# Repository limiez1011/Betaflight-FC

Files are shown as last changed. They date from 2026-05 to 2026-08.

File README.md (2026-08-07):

# yecnod F405 V1.1

## Description

open-source (not that anyone would want to use it) 40x40 F405 Flight controller using betaflight software.
## Features

- 3 Universal UARTS
- Dedicated pads for analog VTX
- 9V and 5V Buck converters
- 2x 3.3V LDOS
- Integrated barometer
- LDO and Buck converter status LEDS
- 16MB Blackbox flash
- Full betaflight support
- ICM 42688-P (kind of a flex with how hard they are to get nowadays)
- 4V5 Pads for RX

This is the first revision of the yecnodF405 so expect more features on the 2nd.

[Schematic PDF](https://github.com/user-attachments/files/29501861/20x20.fc.pdf)

## COST

- AROUND 60 USD PER PCB
- AROUND 30 USD FOR 5 PCBS

On my next revision I will try to cut the costs by atleast 40%

## BOM

| | NAME | PURPOSE | QTY | PRICE  | LINK |
|---|---|---|-----|---|---|
| 1 | LCSC | PASSIVES/ALL IC'S | 1 | $73.43 | [LINK](https://www.lcsc.com) |
| 2 | HOT AIR GUN | SOLDERING | 1 | $35 | [LINK](https://www.emag.ro/fier-de-lipit-torta-cu-aer-cald-yihua-8858-iv-a5dc-582e4/pd/D3JM2VYBM/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) |
| 3 | MP4420 | BUCK CONVERTER (NOT AVAILABLE ON LCSC) | 10  | $7.7 | [LINK](https://www.aliexpress.com/item/1005009928983923.html?spm=a2g0o.cart.0.0.2e1938damlvGFl&mp=1) |
| 4 | TWEEZERS | HELP FOR SOLDERING TINY 0402 | 2 | $16.5  | [LINK](https://www.aliexpress.com/item/1005007691201333.html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) [LINK](https://www.aliexpress.com/item/1005008389644631.html?spm=a2g0o.cart.0.0.2e1938damlvGFl&mp=1) |
| 5 | FLUX | SOLDERING | 1 | $11.2  | [LINK](https://www.aliexpress.com/item/1005008666080401.html?spm=a2g0o.cart.0.0.2e1938damlvGFl&mp=1) |
| 6 | C245 TIP | SOLDERING | 1 | $7 | [LINK](https://www.aliexpress.com/item/1005008666080401.html?spm=a2g0o.cart.0.0.2e1938damlvGFl&mp=1) |
| 7 | JLCPCB | PCBS | 5 | $12.71 | [LINK](https://jlcpcb.com/) |
| 8 | TARIFFS | dumb eu laws | 1 | $41 | |

Final prices for each website are available as screenshots on the macondo website. LCSC cart BOM is available as a csv. 
Total price for everything is 204.73 USD
## Notes

- This is my 2nd ever electronics project (Although I made another 3 during the break I took on this project) so don't expect everything to be electrically sound, this has been a great learning experience though, even with all the headaches it gave me.
- The jlcpcb BOM is only partly complete since I've decided to not use PCBA (use at you own risk some parts may not be right)

## Photos






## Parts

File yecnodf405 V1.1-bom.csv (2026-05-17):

Name | Purpose | Quantity | Total Cost (USD) | Link | Distributor
Solder paste | soldering | 1 | 9.00 | https://www.gsmnet.ro/aparatura-instrumente-service-piese-schimb-consumabile/pasta-fludor-relife-rl-406s-tip-seringa | GSMNET.RO
Solder paste squegee | soldering | 1 | 3.00 | https://ro.farnell.com/chip-quik/minisqueege-1/solder-paste-stencil-squeegee/dp/3549325 | Farnell RO
FLUX PASTE | Soldering components | 1 | 13.00 | https://ro.farnell.com/mg-chemicals/8341-10ml/no-clean-flux-paste-10ml-10g/dp/3018420 | Farnell RO
Fnirsi SAG-55 | Hot air station (soldering) | 1 | 68.00 | https://www.fnirsi.com/products/sag-55?variant=46483610796250 | FNIRSI
PCB+stencil | pcbing+stenciling | 5 | 35.00 |  | JLCPCB
JST-SH 8PIN | esc comms | 1 | 1.50 |  | LCSC
INDUCTORS | BUCK CONVERTERS | 2 | 2.70 |  | FARNELL RO
ICM-42688-P | IMU (should have at home | 1 | 0.00 |  | me
PASSIVES TOTAL COST | TOTAL cost of all caps resistors diodes leds | 1 | 8.50 | https://www.lcsc.com/ | LCSC
C25858 | 16.9K | 2 | 0.00
C1985520 | 16Mhz | 1 | 0.62 | https://www.lcsc.com/product-detail/C1985520.html?s_z=n_q_t_ABM11 | LCSC
C11476 | 18.7k | 1 | 0.00
C11702 | 1K | 2 | 0.00
C1518208 | 1uF | 3 | 0.00
C25150 | 20 | 2 | 0.00
C25092 | 22 | 2 | 0.00
C3845593 | 22uF | 1 | 0.00
C86295 | 22uF | 1 | 0.00
C25769 | 24K | 1 | 0.00
C1985480 | 27Mhz | 1 | 1.66 | https://www.lcsc.com/product-detail/C1985480.html?s_z=n_q_t_ABM11 | LCSC
C12530 | 2u2 | 3 | 0.00
C25900 | 4.7K | 3 | 0.00
C2858031 | 4.7uF | 2 | 0.00
C69335 | 4.7uF | 2 | 0.00
C25118 | 47 | 1 | 0.00
C47339 | 470nF | 1 | 0.00
C76659 | 47uF | 1 | 0.00
C25905 | 5.1K | 2 | 0.00
C25904 | 51.1K | 1 | 0.00
C25130 | 680 | 1 | 0.00
C25133 | 75 | 2 | 0.00
C25798 | 75K | 1 | 0.00
C19709 | 86.6K | 1 | 0.00
C270420 | 9.76K | 1 | 0.00
C3194330 | MP4420GJ-P | 2 | 10.00
C15639 | MS561101BA03-50 | 1 | 6.62 | https://www.lcsc.com/product-detail/C15639.html?s_z=n_q_t_MS5611 | LCSC
C25741 | 100K | 7 | 0.00
C25744 | 10k | 1 | 0.00
C1527 | 150pF | 2 | 0.00
C190862 | W25Q128JVPIQ | 2 | 7.21 | https://www.lcsc.com/product-detail/C190862.html?s_z=n_q_W25Q128JVPIQ | LCSC
C165948 | USCBC | 5 | 0.86 | https://www.lcsc.com/product-detail/C165948.html?s_z=n_q_p_USBC%2520HRO | LCSC
C2054141 | STM32F405RGT6 | 1 | 3.97 | https://www.lcsc.com/product-detail/C15742.html?s_z=n_q_STM32F405RGT6 | LCSC
C82351 | AT7456E | 1 | 3.61 | https://www.lcsc.com/product-detail/C82351.html?s_z=s_p_t_AT7456E | LCSC
C2969892 | LDL212PV33R | 2 | 1.30 | https://www.lcsc.com/product-detail/C2969892.html?s_z=n_q_p_LDL12PV33R | LCSC
C10217 | SMBJ28A | 1 | 0.58 | https://www.lcsc.com/product-detail/C178227.html?s_z=n_q_SMBJ28A | LCSC
C25867 | 1.5K | 1 | 0.00
C14663 | 100nF | 2 | 0.00
C24497 | 100nF | 1 | 0.00
C307331 | 100nF | 18 | 0.00
C307331 | 100nf | 2 | 0.00
C25744 | 10K | 4 | 0.00
C15195 | 10nF | 1 | 0.00
C1548 | 15pF | 2 | 0.00

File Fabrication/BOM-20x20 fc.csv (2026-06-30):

Comment | Designator | Footprint | LCSC | Quantity
1.5K | R29 | R_0402_1005Metric | C25867 | 1
100K | R19,R22,R28,R4,R8 | R_0402_1005Metric | C25741 | 5
100nF | C17,C29,C41 | C_0603_1608Metric | C14663 | 3
100nF | C13,C14,C23,C25,C26,C27,C3,C30,C33,C34,C36,C37,C4,C40,C5,C6,C7,C8 | C_0402_1005Metric | C307331 | 18
100nf | C38,C39 | C_0402_1005Metric | C307331 | 2
10K | R13,R26,R27,R30 | R_0402_1005Metric | C25744 | 4
10k | R35 | R_0402_1005Metric | C25744 | 1
10nF | C22 | C_0402_1005Metric | C15195 | 1
12.4K | R20 | R_0402_1005Metric | C11692 | 1
150K | R10 | R_0402_1005Metric | C25755 | 1
15pF | C10,C11 | C_0402_1005Metric | C1548 | 2
16Mhz | Y1 | CRYSTAL-SMD_4P-L2.0-W1.6-BL | C1985520 | 1
18.7K | R7 | R_0402_1005Metric | C11476 | 1
1K | R31,R32 | R_0402_1005Metric | C11702 | 2
1uF | C18,C20,C9 | C_0402_1005Metric | C1518208 | 3
20 | R18,R5 | R_0402_1005Metric | C25150 | 2
22 | R1,R2 | R_0402_1005Metric | C25092 | 2
22.6K | R6 | R_0402_1005Metric | C477674 | 1
22uF | C15,C32 | C_0805_2012Metric | C45783 | 2
27Mhz | Y2 | CRYSTAL-SMD_4P-L2.0-W1.6-BL | C1985480 | 1
2u2 | C1,C2,C24 | C_0402_1005Metric | C12530 | 3
4.7K | R12,R33,R34 | R_0402_1005Metric | C25900 | 3
4.7uF | C19,C21 | C_0402_1005Metric | C2858031 | 2
4.7uF | C12,C28 | C_0805_2012Metric | C98192 | 2
47 | R15 | R_0402_1005Metric | C25118 | 1
470nF | C35 | C_0402_1005Metric | C47339 | 1
47uF | C42 | C_1206_3216Metric | C76659 | 1
5.1K | R3,R36 | R_0402_1005Metric | C25905 | 2
680 | R14 | R_0402_1005Metric | C137948 | 1
75 | R24,R25 | R_0402_1005Metric | C2909384 | 2
8.66K | R21 | R_0402_1005Metric | C5126133 | 1
D_Schottky | D2,D3 | D_0603_1608Metric | C151629 | 2
FerriteBead_Small | FB1 | L_0402_1005Metric | C160977 | 1
ICM-42688-P | U2 | LGA-14_L3.0-W2.5-P0.50-TL | C1850418 | 1
LDL212PV33R | U8,U9 | DFN-6_L2.0-W2.0-P0.50-BL-EP1.45 | C2969892 | 2
LED | D4,D5,D6,D7 | LED_0603_1608Metric | C2288 | 4
LED GREEN | D8 | LED_0603_1608Metric | C12624 | 1
MAX7456EUI_ | U3 | TSSOP-28_L9.7-W4.4-P0.65-LS6.4-BL-EP-2 | C82351 | 1
MP4420GJ-P | U4,U7 | TSOT-23-8_L2.9-W1.6-P0.65-LS2.8-BL | C3194330 | 2
MS561101BA03-50 | A1 | SENSORS-SMD_MS5611-01BA03 | C15639 | 1
SMBJ28A | D1 | D_SMA | C19077582 | 1
SMHT4020-100MT | L3,L4 | IND-SMD_L4.0-W4.0_TNR4030S | C42924178 | 2
STM32F405RGTx | U1 | LQFP-64_10x10mm_P0.5mm | C2054141 | 1
USB_C_Receptacle_USB2.0_14P | J1 | USB_C_Receptacle_HRO_TYPE-C-31-M-12 | C165948 | 1
W25Q128JVPIQ | U5 | WSON-8_L6.0-W5.0-P1.27-BL-EP | C190862 | 1
jst sh | J2 | JST_SH_SM08B-SRSS-TB_1x08-1MP_P1.00mm_Horizontal | C160407 | 1
RX3 | TP11 | 1.5mm pad |  | 1
GND | TP24 | 1.5mm pad |  | 1
+5V | TP21 | 1.5mm pad |  | 1
GND | TP16 | 1.5mm pad |  | 1
+9V | TP17 | 1.5mm pad |  | 1
GND | TP23 | 1.5mm pad |  | 1
+5V | TP14 | 1.5mm pad |  | 1
CAM | TP15 | 1.5mm pad |  | 1
GND | TP9 | 1.5mm pad |  | 1
4V5 | TP8 | 1.5mm pad |  | 1
GND | TP5 | 1.5mm pad |  | 1
VID | TP19 | 1.5mm pad |  | 1
4V5 | TP13 | 1.5mm pad |  | 1
4V5 | TP10 | 1.5mm pad |  | 1
SA | TP18 | 1.5mm pad |  | 1
+5V | TP22 | 1.5mm pad |  | 1
+9V | TP20 | 1.5mm pad |  | 1
4V5 | TP6 | 1.5mm pad |  | 1
TX3 | TP12 | 1.5mm pad |  | 1
NANOT240AS | S1 | NANOT240AS |  | 1
4V5 | TP7 | 1.5mm pad |  | 1

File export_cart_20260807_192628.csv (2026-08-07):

Index | LCSC# | MPN | Manufacturer | Package | Customer # | Description | RoHS | Quantity | MOQ | Multiple | Unit Price($) | Extended Price($) | Product Link
1 | C160977 | BLM15PX601SN1D | muRata | 0402 |  | 600Ω@100MHz 1 Line Ferrite Bead 0402 900mA 230mΩ | yes | 50 | 50 | 50 | 0.0127 | 0.64 | https://www.lcsc.com/product-detail/C160977.html
2 | C137973 | RC0402FR-0747RL | YAGEO | 0402 |  | 47Ω 62.5mW 50V Thick Film Resistor ±100ppm/℃ ±1% 0402 Chip Resistor - Surface Mount RoHS | yes | 100 | 100 | 100 | 0 | 0 | https://www.lcsc.com/product-detail/C137973.html
3 | C88946 | GRM155R71A474KE01D | muRata | 0402 |  | 470nF ±10% 10V Ceramic Capacitor X7R 0402 | yes | 20 | 20 | 20 | 0.0353 | 0.71 | https://www.lcsc.com/product-detail/C88946.html
4 | C22367834 | HGC1206R5226M350NSPJ | Chinocera | 1206 |  | 22uF ±20% 35V Ceramic Capacitor X5R 1206 | yes | 5 | 5 | 5 | 0 | 0 | https://www.lcsc.com/product-detail/C22367834.html
5 | C186154 | RN73H1ETTP5101B25 | KOA | 0402 |  | 5.1kΩ 62.5mW 50V Metal Film Resistor ±25ppm/℃ ±0.1% 0402 Chip Resistor - Surface Mount RoHS | yes | 5 | 5 | 5 | 0.1824 | 0.91 | https://www.lcsc.com/product-detail/C186154.html
6 | C137948 | RC0402FR-07680RL | YAGEO | 0402 |  | 680Ω 62.5mW 50V Thick Film Resistor ±100ppm/℃ ±1% 0402 Chip Resistor - Surface Mount RoHS | yes | 100 | 100 | 100 | 0 | 0 | https://www.lcsc.com/product-detail/C137948.html
7 | C2909384 | FRC0402F75R0TS | FOJAN | 0402 |  | 75Ω ±1% 62.5mW 0402 Thick Film Resistor | yes | 100 | 100 | 100 | 0.0022 | 0.22 | https://www.lcsc.com/product-detail/C2909384.html
8 | C5126133 | FRC0402F8661TS | FOJAN | 0402 |  | 8.66kΩ ±1% 62.5mW 0402 Thick Film Resistor | yes | 100 | 100 | 100 | 0.0019 | 0.19 | https://www.lcsc.com/product-detail/C5126133.html
9 | C151629 | SDM02U30LP3-7B | DIODES | X3-DFN0603-2 |  | 1 Independent 30V 370mV@10mA 100mA X3-DFN0603-2 Single Diodes RoHS | yes | 10 | 10 | 10 | 0.0643 | 0.64 | https://www.lcsc.com/product-detail/C151629.html
10 | C728576 | RT0402FRE07100KL | YAGEO | 0402 |  | 100kΩ 62.5mW 50V Thin Film Resistor ±50ppm/℃ ±1% 0402 Chip Resistor - Surface Mount RoHS | yes | 50 | 50 | 50 | 0.0210 | 1.05 | https://www.lcsc.com/product-detail/C728576.html
11 | C2288 | KT-0603B | Hubei KENTO Elec | 0603 |  | Blue 469nm LED Indication - Discrete 3.1V 0603 | yes | 50 | 50 | 50 | 0.0103 | 0.52 | https://www.lcsc.com/product-detail/C2288.html
12 | C12624 | KT-0603G | Hubei KENTO Elec | 0603 |  | Emerald Green 525nm LED Indication - Discrete 3.1V 0603 | yes | 50 | 50 | 50 | 0.0122 | 0.61 | https://www.lcsc.com/product-detail/C12624.html
13 | C82351 | AT7456E | ZHONGKEWEI | TSSOP-28-EP |  | TSSOP-28-EP Microcontrollers RoHS | yes | 1 | 1 | 1 | 3.7445 | 3.74 | https://www.lcsc.com/product-detail/C82351.html
14 | C15639 | MS561101BA03-50 | TE Connectivity | QFN-8(3x5) |  | 1Kpa~1.2bar QFN-8(3x5) Pressure Sensors, Transducers RoHS | yes | 1 | 1 | 1 | 6.7122 | 6.71 | https://www.lcsc.com/product-detail/C15639.html
15 | C19077582 | SMBJ28A | R+O | DO-214AA(SMB) |  | 45.4VC Clamp 13.22A@10/1000us Ipp TVS DIODE DO-214AA(SMB) | yes | 5 | 5 | 5 | 0.0498 | 0.25 | https://www.lcsc.com/product-detail/C19077582.html
16 | C42924178 | SMHT4020-100MT | Shun Xiang Nuo | SMD,4x4mm |  | 2A 10uH ±20% 2.8A 220mΩ SMD,4x4mm Fixed Inductors RoHS | yes | 10 | 10 | 10 | 0.0532 | 0.53 | https://www.lcsc.com/product-detail/C42924178.html
17 | C165948 | TYPE-C-31-M-12 | Korean Hroparts Elec | SMD |  | USB-C (USB TYPE-C) Receptacle Connector 16 Position Surface Mount | yes | 5 | 5 | 5 | 0.1709 | 0.85 | https://www.lcsc.com/product-detail/C165948.html
18 | C160407 | SM08B-SRSS-TB(LF)(SN) | JST | SMD,P=1mm,Surface Mount,Right Angle |  | Connector Header 8 position 1mm Pitch 1A Surface Mount, Right Angle -25℃~+85℃ | yes | 5 | 5 | 5 | 0.3314 | 1.66 | https://www.lcsc.com/product-detail/C160407.html
19 | C2858031 | GRM155R61E475ME15D | muRata | 0402 |  | 4.7uF ±20% 25V Ceramic Capacitor X5R 0402 | yes | 20 | 5 | 5 | 0.1512 | 3.02 | https://www.lcsc.com/product-detail/C2858031.html
20 | C2933074 | FRC0402F1501TS | FOJAN | 0402 |  | 1.5kΩ ±1% 62.5mW 0402 Thick Film Resistor | yes | 100 | 100 | 100 | 0.0022 | 0.22 | https://www.lcsc.com/product-detail/C2933074.html
21 | C152814 | 0402B104K500CT | Walsin | 0402 |  | 100nF ±10% 50V Ceramic Capacitor X7R 0402 | yes | 200 | 50 | 50 | 0.0110 | 2.20 | https://www.lcsc.com/product-detail/C152814.html
22 | C17702748 | C0603B104J500NT | TORCH | 0603 |  | 100nF ±5% 50V Ceramic Capacitor X7R 0603 | yes | 5 | 5 | 5 | 0.0436 | 0.22 | https://www.lcsc.com/product-detail/C17702748.html
23 | C191984 | CRCW040210K0JNED | VISHAY | 0402 |  | 63mW 10kΩ 50V Thick Film Resistor ±5% ±200ppm/℃ 0402 Chip Resistor - Surface Mount RoHS | yes | 200 | 100 | 100 | 0.0041 | 0.82 | https://www.lcsc.com/product-detail/C191984.html
24 | C11692 | 0402WGF1242TCE | UNI-ROYAL | 0402 |  | 12.4kΩ ±1% 62.5mW 0402 Thick Film Resistor | yes | 100 | 100 | 100 | 0.0032 | 0.32 | https://www.lcsc.com/product-detail/C11692.html
25 | C54920729 | HRC0402J154 DNTO | HWA CHN | 0402 |  | 62.5mW 150kΩ 50V Thick Film Resistor ±5% ±100ppm/℃ 0402 Chip Resistor - Surface Mount RoHS | yes | 100 | 100 | 100 | 0.0006 | 0.06 | https://www.lcsc.com/product-detail/C54920729.html
26 | C1548 | 0402CG150J500NT | FH | 0402 |  | 15pF ±5% 50V Ceramic Capacitor C0G 0402 | yes | 100 | 100 | 100 | 0.0047 | 0.47 | https://www.lcsc.com/product-detail/C1548.html
27 | C1985520 | ABM11-16.000MHZ-B7G-T | ABRACON | SMD2016-4P |  | Crystal 16MHz ±15ppm 10pF 150Ω SMD2016-4P | yes | 1 | 1 | 1 | 0.8265 | 0.83 | https://www.lcsc.com/product-detail/C1985520.html
28 | C11476 | 0402WGF1872TCE | UNI-ROYAL | 0402 |  | 18.7kΩ ±1% 62.5mW 0402 Thick Film Resistor | yes | 100 | 100 | 100 | 0.0035 | 0.35 | https://www.lcsc.com/product-detail/C11476.html
29 | C852624 | RT0402BRD071KL | YAGEO | 0402 |  | 1kΩ 62.5mW 50V Thin Film Resistor ±25ppm/℃ ±0.1% 0402 Chip Resistor - Surface Mount RoHS | yes | 50 | 50 | 50 | 0.0271 | 1.36 | https://www.lcsc.com/product-detail/C852624.html
30 | C77006 | GRM155R61C105KA12D | muRata | 0402 |  | 1uF ±10% 16V Ceramic Capacitor X5R 0402 | yes | 100 | 50 | 50 | 0.0301 | 3.01 | https://www.lcsc.com/product-detail/C77006.html
31 | C477674 | RC0402FR-0722K6L | YAGEO | 0402 |  | 22.6kΩ 62.5mW 50V Thick Film Resistor ±100ppm/℃ ±1% 0402 Chip Resistor - Surface Mount RoHS | yes | 100 | 100 | 100 | 0.0031 | 0.31 | https://www.lcsc.com/product-detail/C477674.html
32 | C338078 | C2012X5R1E226MT000E | TDK | 0805 |  | 22uF ±20% 25V Ceramic Capacitor X5R 0805 | yes | 2 | 1 | 1 | 0.3199 | 0.64 | https://www.lcsc.com/product-detail/C338078.html
33 | C1985480 | ABM11-27.000MHZ-D2X-T3 | ABRACON | SMD2016-4P |  | ±20ppm 10pF ±20ppm SMD2016-4P Crystals RoHS | yes | 2 | 1 | 1 | 1.6645 | 3.33 | https://www.lcsc.com/product-detail/C1985480.html
34 | C12530 | CL05A225MQ5NSNC | Samsung Electro-Mechanics | 0402 |  | 2.2uF ±20% 6.3V Ceramic Capacitor X5R 0402 | yes | 100 | 100 | 100 | 0.0065 | 0.65 | https://www.lcsc.com/product-detail/C12530.html
35 | C98192 | CL21A475KBQNNNE | Samsung Electro-Mechanics | 0805 |  | 4.7uF ±10% 50V Ceramic Capacitor X5R 0805 | yes | 10 | 10 | 10 | 0.1216 | 1.22 | https://www.lcsc.com/product-detail/C98192.html
36 | C15742 | STM32F405RGT6 | ST | LQFP-64(10x10) |  | ARM Cortex-M4 32 Bit 168MHz 51 LQFP-64(10x10) Microcontrollers RoHS | yes | 1 | 1 | 1 | 6.6712 | 6.67 | https://www.lcsc.com/product-detail/C15742.html
37 | C100042 | CC0603KRX7R9BB103 | YAGEO | 0603 |  | 10nF ±10% 50V Ceramic Capacitor X7R 0603 | yes | 50 | 50 | 50 | 0.0151 | 0.76 | https://www.lcsc.com/product-detail/C100042.html
38 | C2906941 | FRC0402J472 TS | FOJAN | 0402 |  | 4.7kΩ ±5% 62.5mW 0402 Thick Film Resistor | yes | 100 | 100 | 100 | 0.0017 | 0.17 | https://www.lcsc.com/product-detail/C2906941.html
39 | C42931809 | ABC02K20R0FT | FH | 0402 |  | 20Ω 62.5mW Thick Film Resistor ±100ppm/℃ ±1% 0402 Chip Resistor - Surface Mount RoHS | yes | 100 | 100 | 100 | 0.0017 | 0.17 | https://www.lcsc.com/product-detail/C42931809.html
40 | C916392 | SS8050 | JSMSEMI | SOT-23 |  | Bipolar (BJT) Transistor NPN 25V 1.5A 300mW Surface Mount SOT-23 | yes | 50 | 50 | 50 | 0.0099 | 0.50 | https://www.lcsc.com/product-detail/C916392.html
41 | C2969892 | LDL212PV33R | ST | DFN-6(2x2) |  | 3.3V Positive Fixed DFN-6(2x2) Voltage Regulators - Linear, Low Drop Out (LDO) Regulators RoHS | yes | 2 | 1 | 1 | 9.6535 | 19.31 | https://www.lcsc.com/product-detail/C2969892.html
42 | C190862 | W25Q128JVPIQ | Winbond | WSON-8-EP(5x6) |  | 128Mbit 2.7V~3.6V 133MHz SPI WSON-8-EP(5x6) Memory RoHS | yes | 1 | 1 | 1 | 3.7478 | 3.75 | https://www.lcsc.com/product-detail/C190862.html

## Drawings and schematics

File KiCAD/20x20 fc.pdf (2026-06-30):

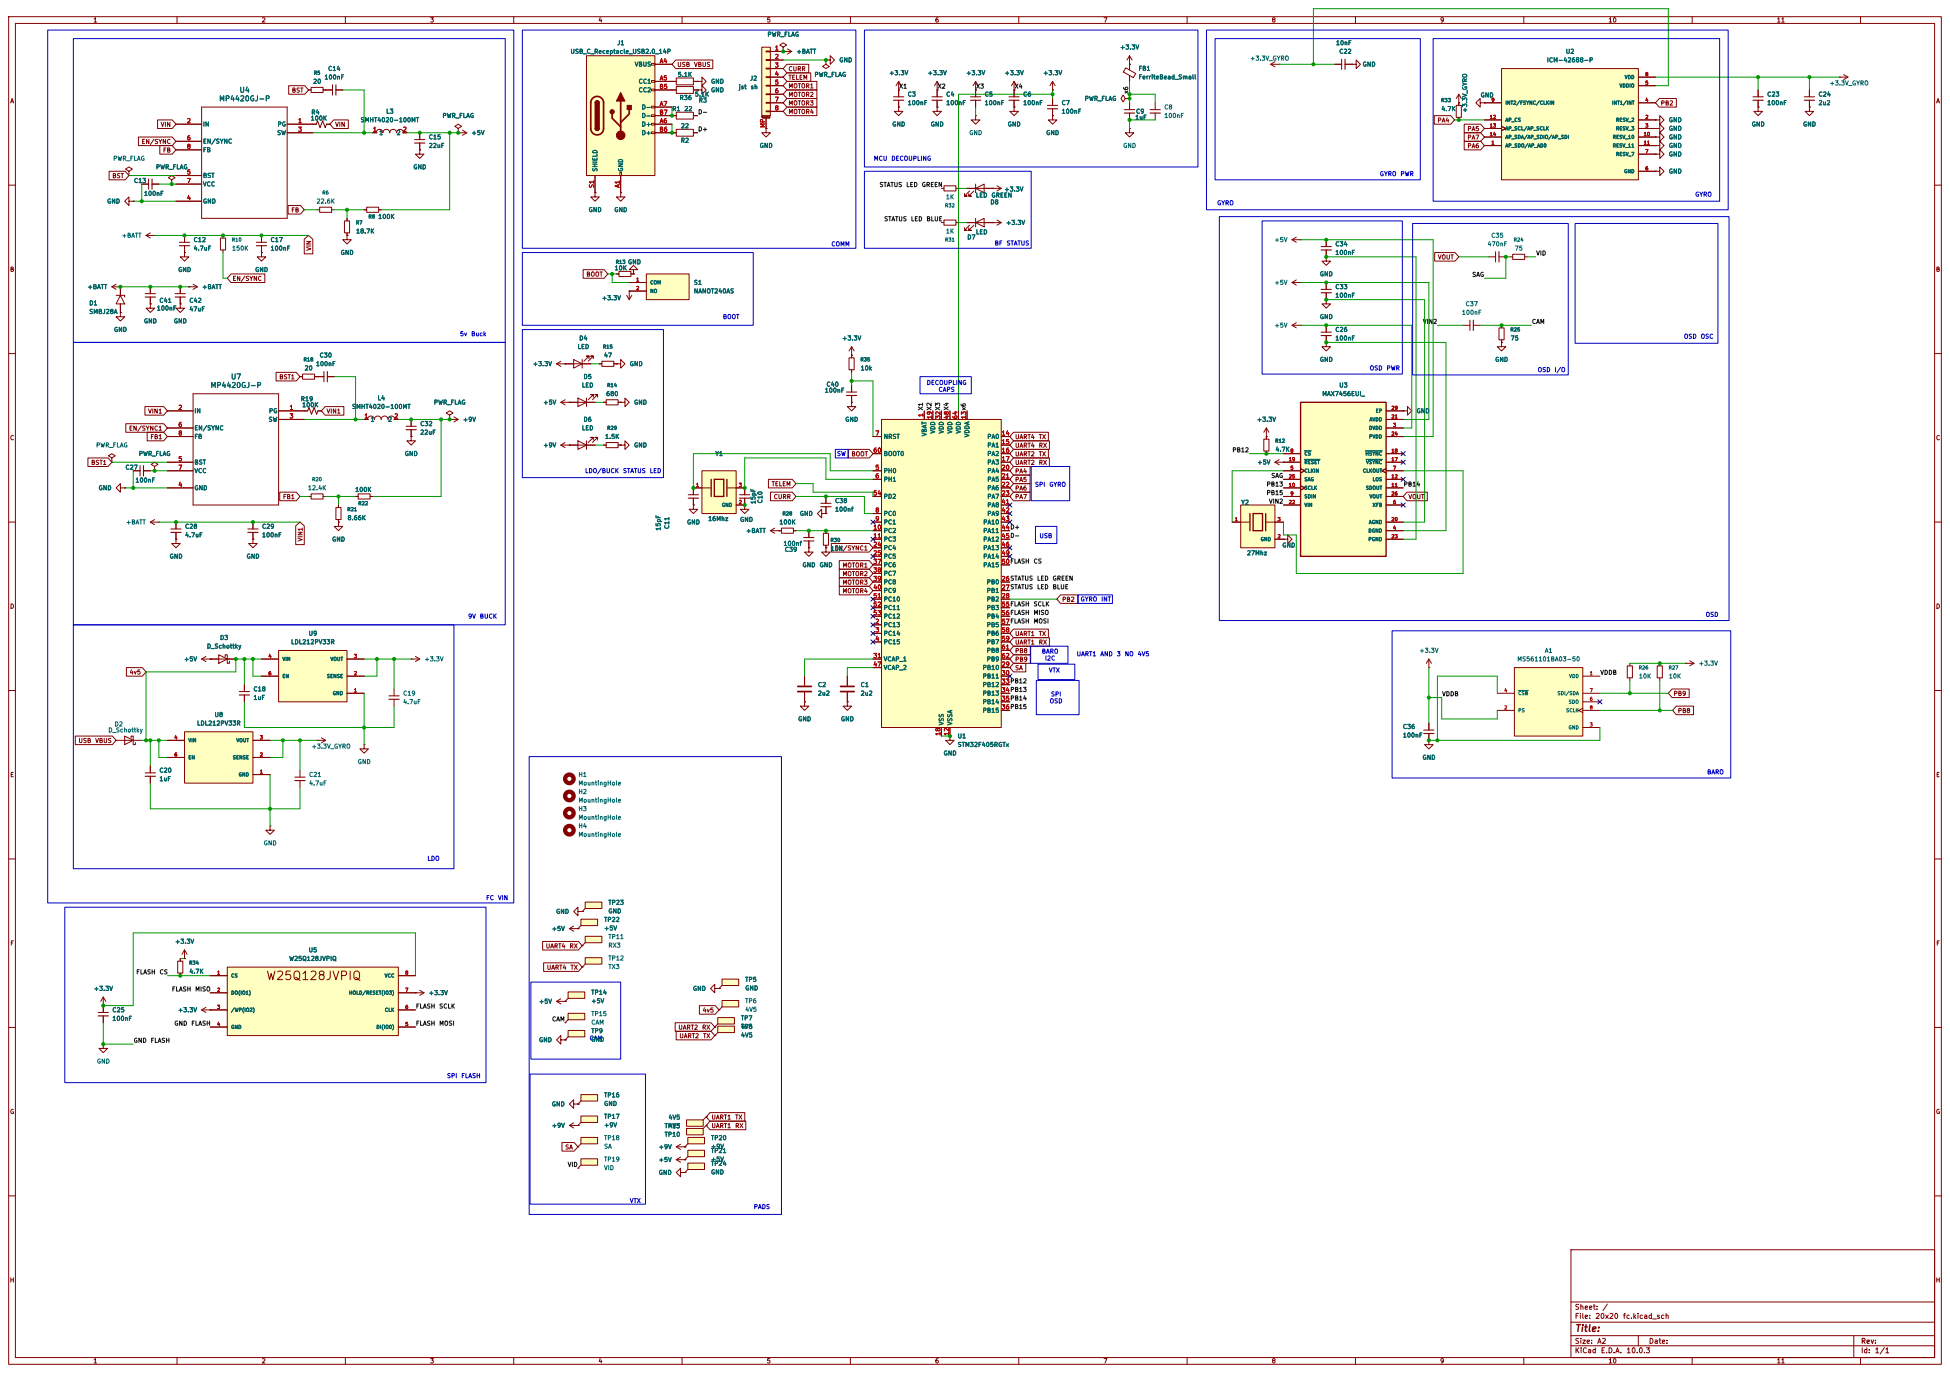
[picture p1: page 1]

STATUS LED BLUE GND FLASH

UART1 TX UART1 RX UART2 TX UART2 RX

Size: A2 | Rev:
KiCad E.D.A. 10.0.3 | Id: 1/1

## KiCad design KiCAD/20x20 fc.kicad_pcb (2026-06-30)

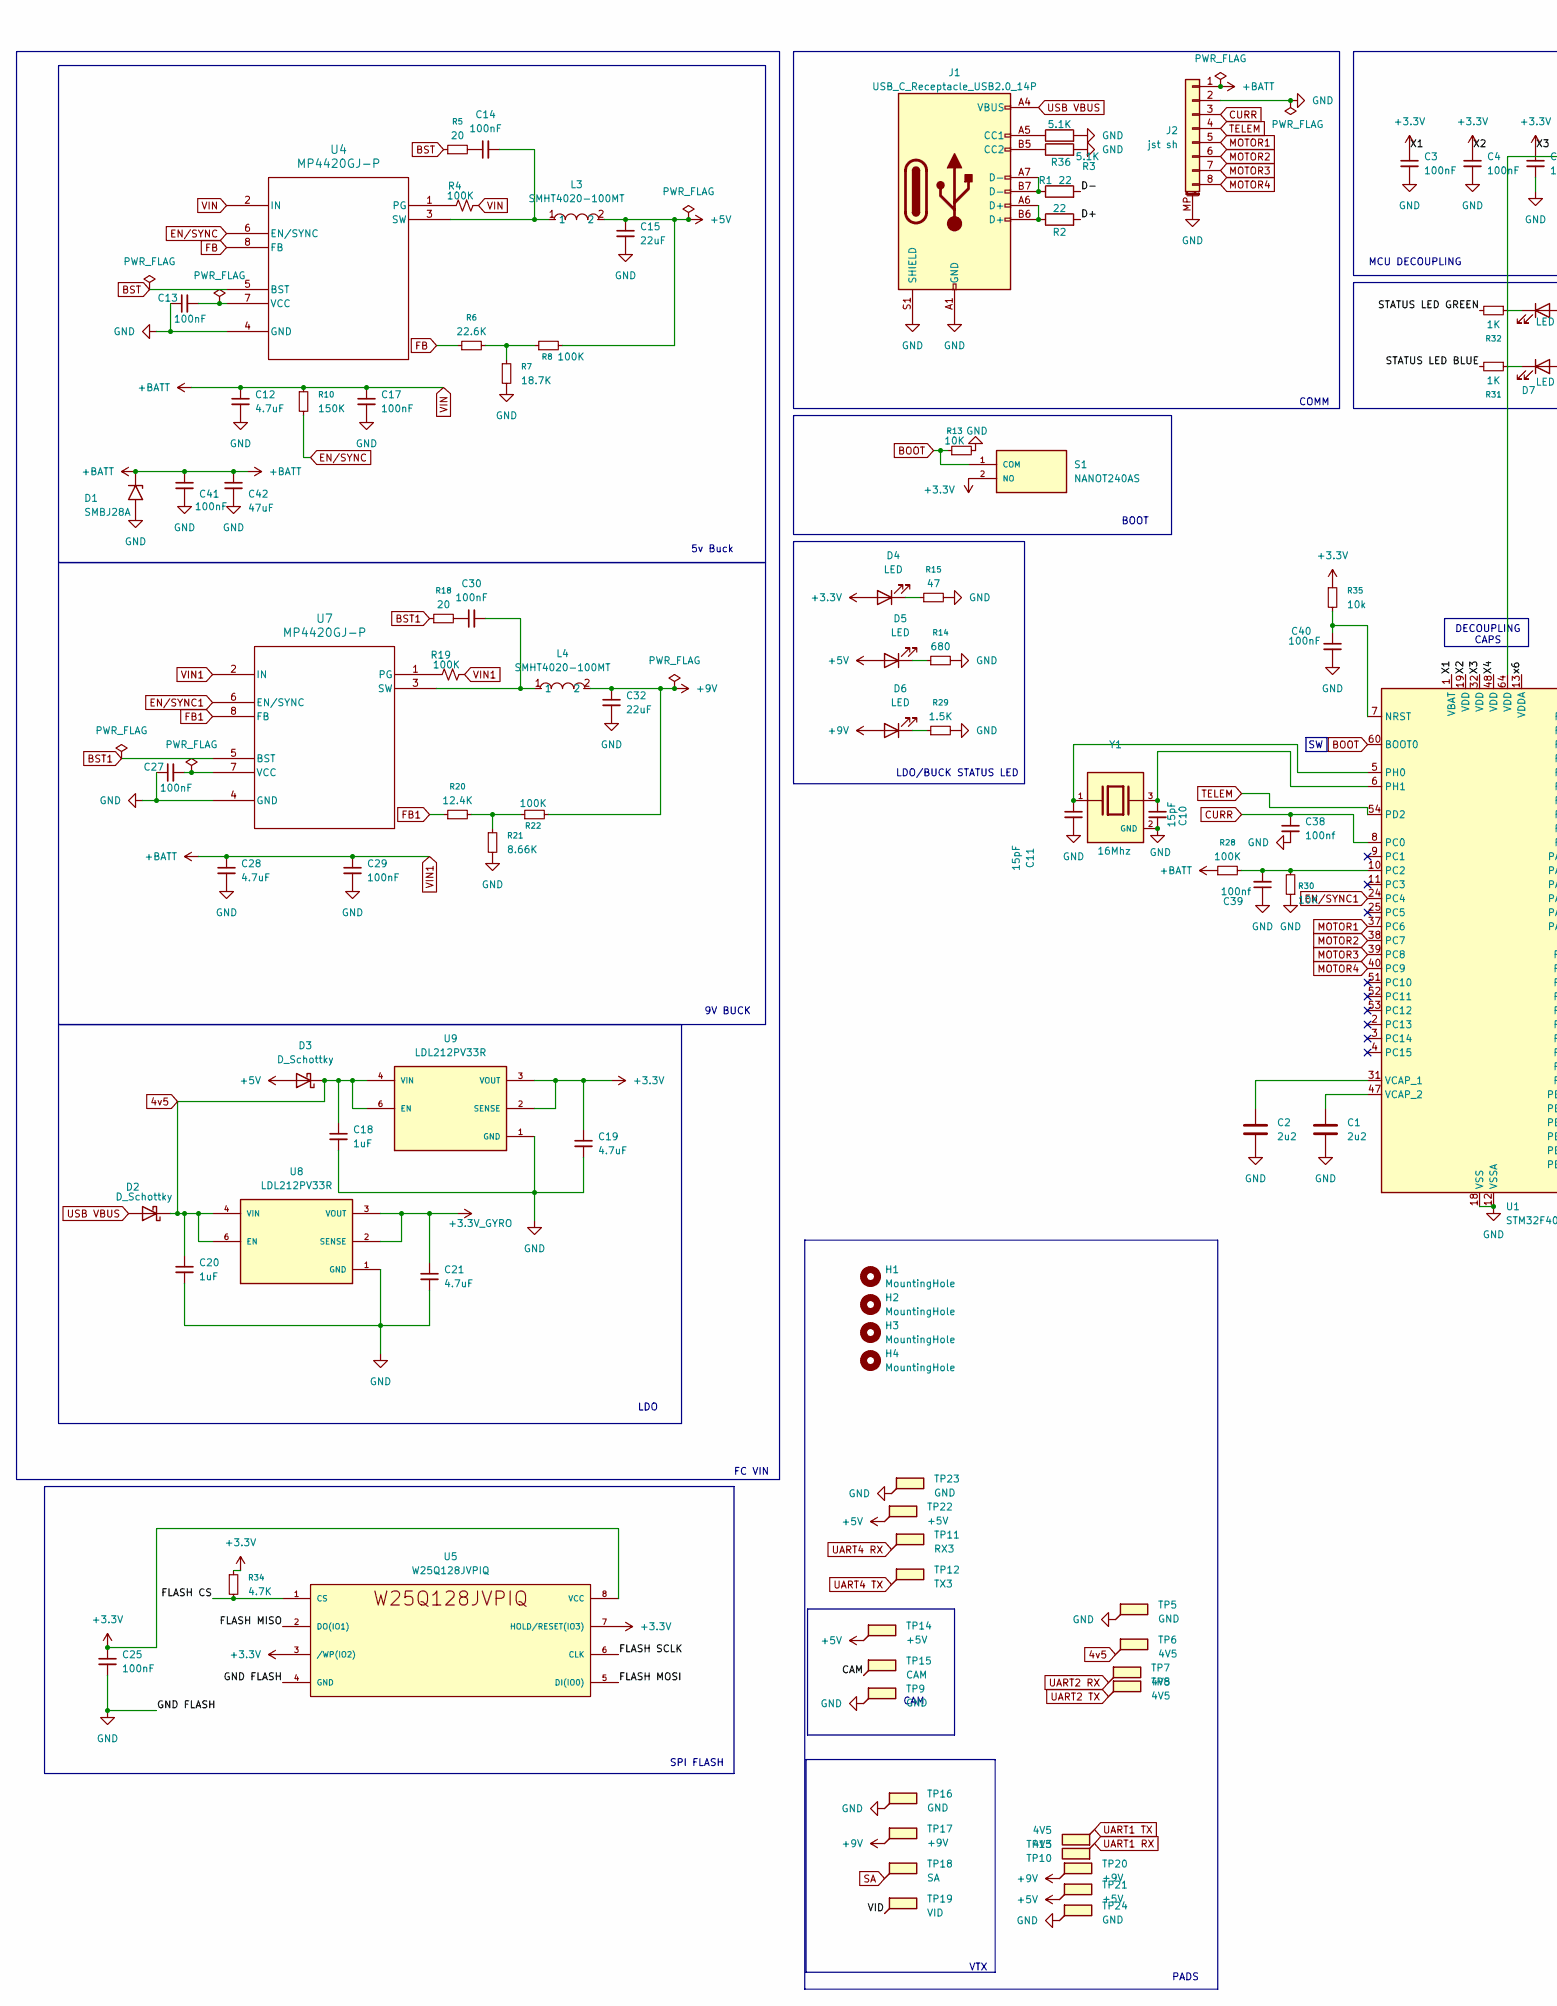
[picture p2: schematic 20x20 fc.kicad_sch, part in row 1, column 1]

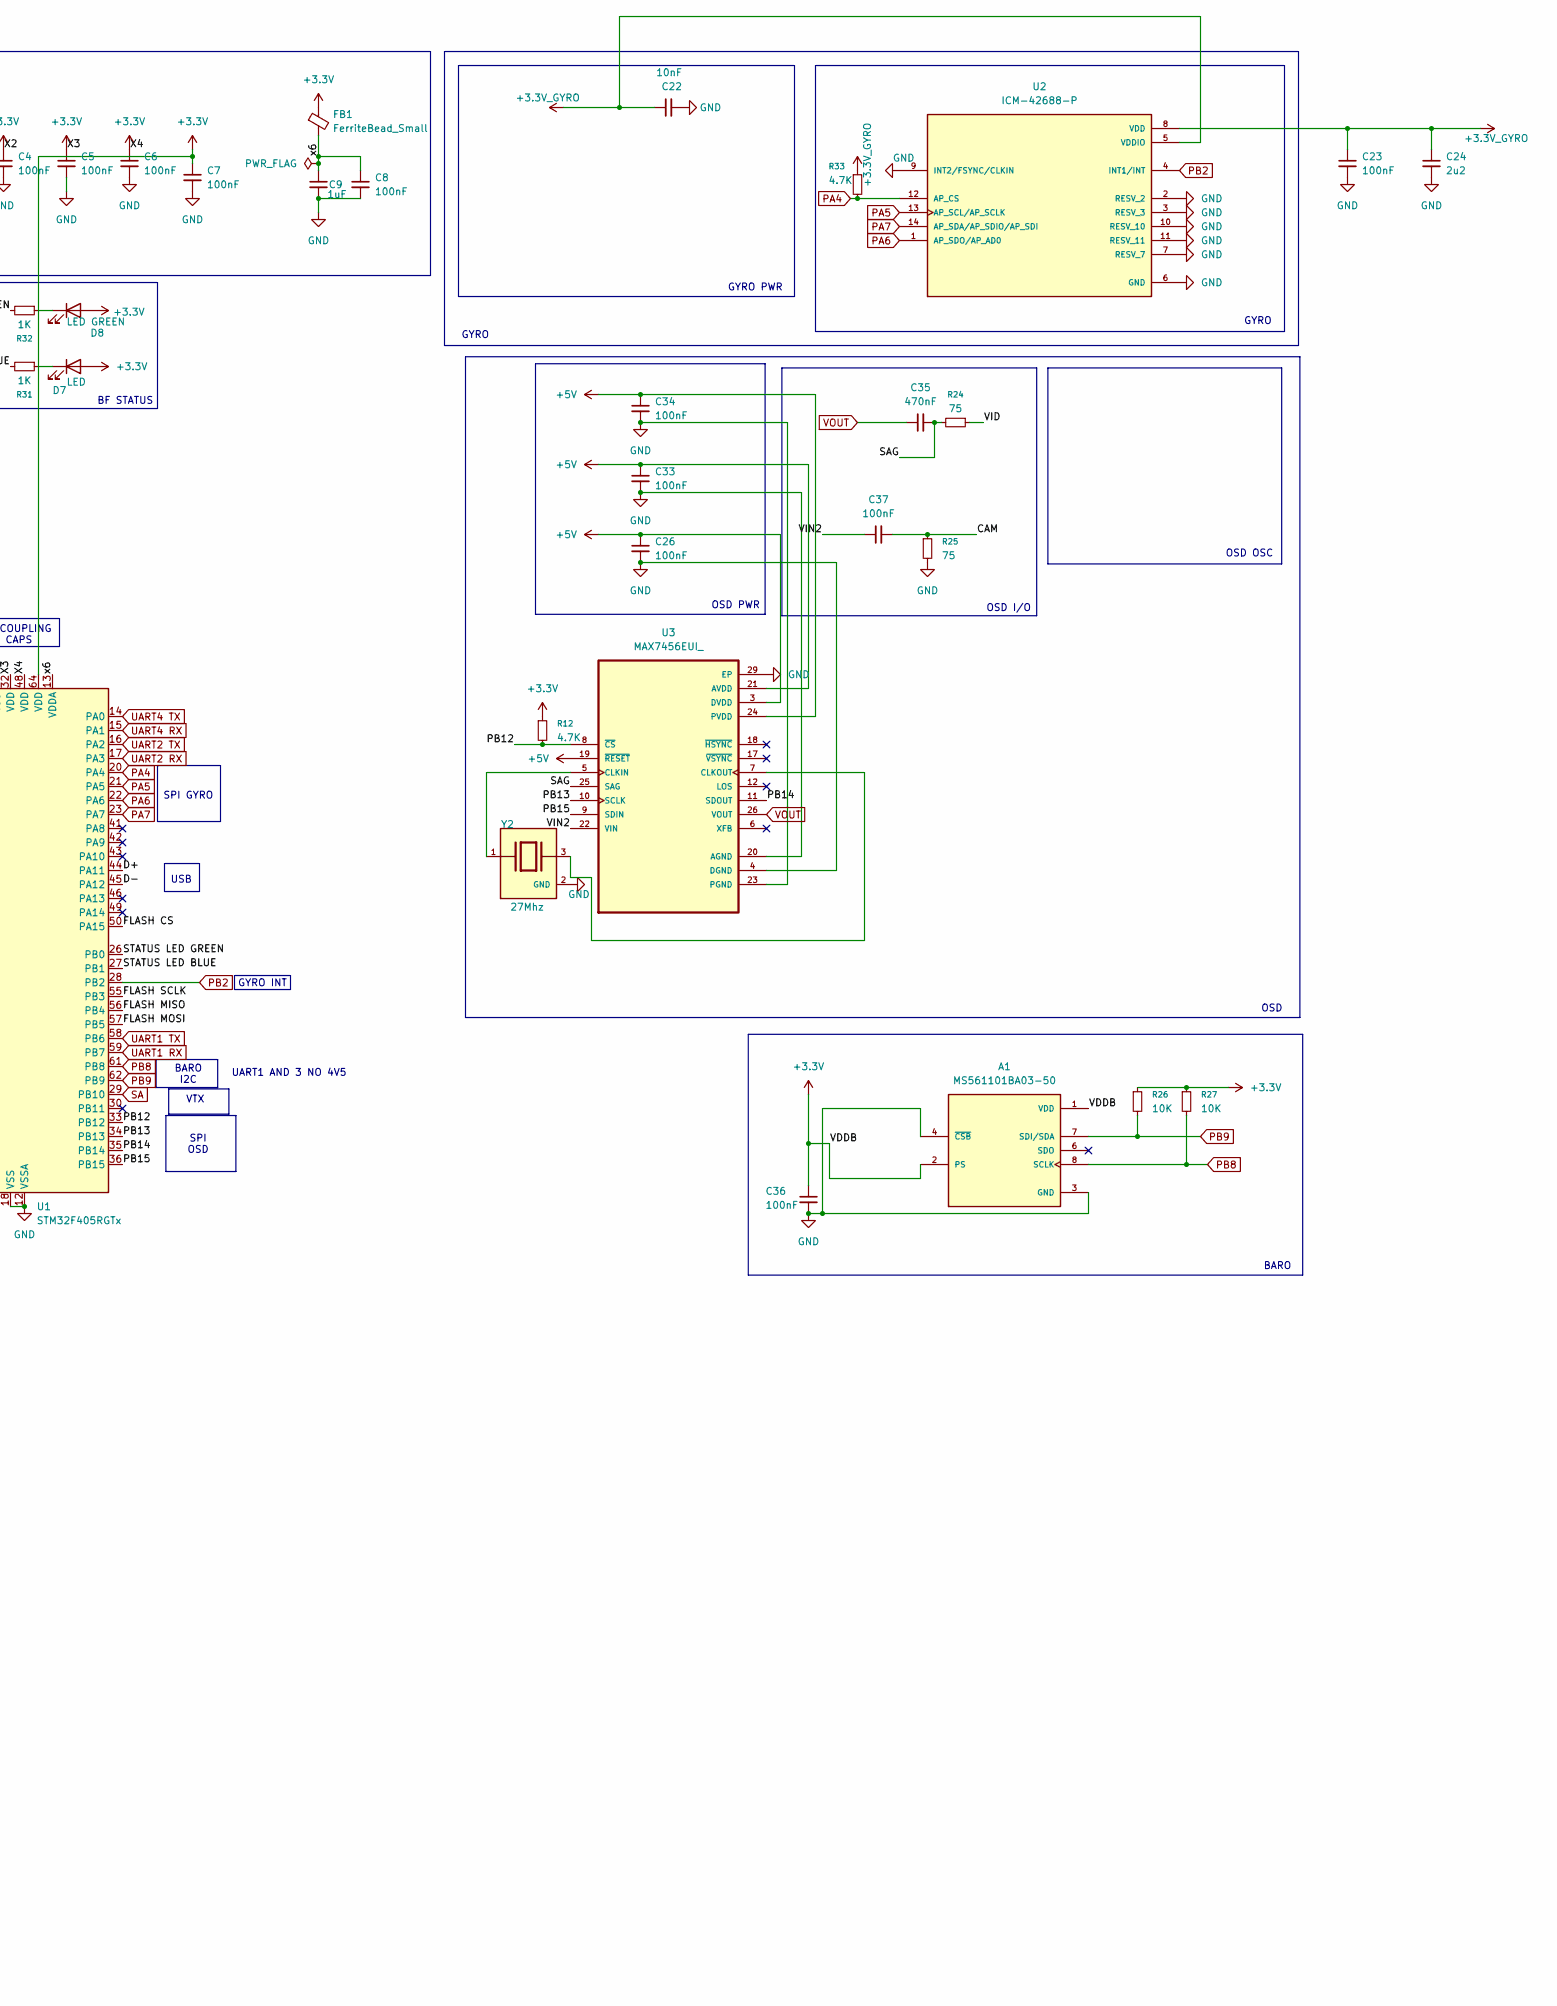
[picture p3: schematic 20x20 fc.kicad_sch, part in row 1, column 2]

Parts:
A1: MS561101BA03-50; SENSORS-SMD_MS5611-01BA03; PARTREV 06/2017
C1, C2, C24: 2u2; C_0402_1005Metric
C3, C4, C5, C6, C7, C8, C13, C14, C23, C25, C26, C27, C30, C33, C34, C36, C37, C40: 100nF; C_0402_1005Metric
C9, C18, C20: 1uF; C_0402_1005Metric
C10, C11: 15pF; C_0402_1005Metric
C12, C28: 4.7uF; C_0805_2012Metric
C15, C32: 22uF; C_0805_2012Metric
C17, C29, C41: 100nF; C_0603_1608Metric
C19, C21: 4.7uF; C_0402_1005Metric
C22: 10nF; C_0402_1005Metric
C35: 470nF; C_0402_1005Metric
C38, C39: 100nf; C_0402_1005Metric
C42: 47uF; C_1206_3216Metric
D1: SMBJ28A; D_SMA
D2, D3: D_Schottky; D_0603_1608Metric
D4, D5, D6, D7: LED; LED_0603_1608Metric
D8: LED GREEN; LED_0603_1608Metric
FB1: FerriteBead_Small; L_0402_1005Metric
H1, H2, H3, H4: MountingHole; MountingHole_4.3mm_M4
J1: USB_C_Receptacle_USB2.0_14P; USB_C_Receptacle_HRO_TYPE-C-31-M-12
J2: jst sh; JST_SH_SM08B-SRSS-TB_1x08-1MP_P1.00mm_Horizontal
L3, L4: SMHT4020-100MT; IND-SMD_L4.0-W4.0_TNR4030S; MPN SMHT4020-100MT; LCSC Part C42924178
R1, R2: 22; R_0402_1005Metric
R3, R36: 5.1K; R_0402_1005Metric
R4, R8, R19, R22, R28: 100K; R_0402_1005Metric
R5, R18: 20; R_0402_1005Metric
R6: 22.6K; R_0402_1005Metric
R7: 18.7K; R_0402_1005Metric
R10: 150K; R_0402_1005Metric
R12, R33, R34: 4.7K; R_0402_1005Metric
R13, R26, R27, R30: 10K; R_0402_1005Metric
R14: 680; R_0402_1005Metric
R15: 47; R_0402_1005Metric
R20: 12.4K; R_0402_1005Metric
R21: 8.66K; R_0402_1005Metric
R24, R25: 75; R_0402_1005Metric
R29: 1.5K; R_0402_1005Metric
R31, R32: 1K; R_0402_1005Metric
R35: 10k; R_0402_1005Metric
S1: NANOT240AS; MANUFACTURER_PART_NUMBER NANOT240AS
TP5, TP9, TP16, TP23, TP24: GND; 1.5mm pad
TP6, TP7, TP8, TP10, TP13: 4V5; 1.5mm pad
TP11: RX3; 1.5mm pad
TP12: TX3; 1.5mm pad
TP14, TP21, TP22: +5V; 1.5mm pad
TP15: CAM; 1.5mm pad
TP17, TP20: +9V; 1.5mm pad
TP18: SA; 1.5mm pad
TP19: VID; 1.5mm pad
U1: STM32F405RGTx; LQFP-64_10x10mm_P0.5mm
U2: ICM-42688-P; LGA-14_L3.0-W2.5-P0.50-TL; PARTREV 1.2
U3: MAX7456EUI_; TSSOP-28_L9.7-W4.4-P0.65-LS6.4-BL-EP-2
U4, U7: MP4420GJ-P; TSOT-23-8_L2.9-W1.6-P0.65-LS2.8-BL
U5: W25Q128JVPIQ; WSON-8_L6.0-W5.0-P1.27-BL-EP
U8, U9: LDL212PV33R; DFN-6_L2.0-W2.0-P0.50-BL-EP1.45; PARTREV 5
Y1: 16Mhz; CRYSTAL-SMD_4P-L2.0-W1.6-BL; PARTREV 06.19.15
Y2: 27Mhz; CRYSTAL-SMD_4P-L2.0-W1.6-BL; PARTREV 06.19.15

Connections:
4v5: C18.1, C20.1, D2.1 (K), D3.1 (K), TP6.1 (1_1), U8.4 (VIN), U8.6 (EN), U9.4 (VIN), U9.6 (EN)
+3.3V: A1.1 (VDD), A1.2 (PS), C3.1, C4.1, C5.1, C6.1, C7.1, C19.1, C25.1, C36.1, D4.2 (A), D7.2 (A), D8.2 (A), FB1.1, R12.1, R26.1, R27.1, R34.1, R35.1, S1.2 (NO), U1.1 (VBAT), U1.19 (VDD), U1.32 (VDD), U1.48 (VDD), U1.64 (VDD), U5.3 (/WP(IO2)), U5.7 (HOLD/RESET(IO3)), U5.8 (VCC), U9.2 (SENSE), U9.3 (VOUT)
+3.3V_GYRO: C21.1, C22.1, C23.1, C24.1, R33.1, U2.5 (VDDIO), U2.8 (VDD), U8.2 (SENSE), U8.3 (VOUT)
+5V: C15.1, C26.1, C33.1, C34.1, D3.2 (A), D5.2 (A), L3.2, R8.2, TP14.1 (1_1), TP21.1 (1_1), TP22.1 (1_1), U3.3 (DVDD), U3.19 (~RESET), U3.21 (AVDD), U3.24 (PVDD)
+9V: C32.1, D6.2 (A), L4.2, R22.2, TP17.1 (1_1), TP20.1 (1_1)
/CAM: C37.2, R25.1, TP15.1 (1_1)
/D+: R2.2, U1.44 (PA11)
/D-: R1.2, U1.45 (PA12)
/FLASH CS: R34.2, U1.50 (PA15), U5.1 (CS)
/FLASH MISO: U1.56 (PB4), U5.2 (DO(IO1))
/FLASH MOSI: U1.57 (PB5), U5.5 (DI(IO0))
/FLASH SCLK: U1.55 (PB3), U5.6 (CLK)
/PB12: R12.2, U1.33 (PB12), U3.8 (~CS)
/PB13: U1.34 (PB13), U3.10 (SCLK)
/PB14: U1.35 (PB14), U3.11 (SDOUT)
/PB15: U1.36 (PB15), U3.9 (SDIN)
/SAG: C35.2, R24.2, U3.25 (SAG)
/STATUS LED BLUE: R31.2, U1.27 (PB1)
/STATUS LED GREEN: R32.2, U1.26 (PB0)
/VID: R24.1, TP19.1 (1_1)
/VIN2: C37.1, U3.22 (VIN)
/x6: C8.1, C9.1, FB1.2, U1.13 (VDDA)
BOOT: R13.1, S1.1 (COM), U1.60 (BOOT0)
BST: R5.1, U4.5 (BST)
BST1: R18.1, U7.5 (BST)
CURR: C38.1, J2.3, U1.8 (PC0)
EN/SYNC: R10.2, U4.6 (EN/SYNC)
EN/SYNC1: U1.24 (PC4), U7.6 (EN/SYNC)
FB: R6.1, U4.8 (FB)
FB1: R20.1, U7.8 (FB)
GND: A1.3 (GND), A1.4 (~CSB), A1.5 (~CSB), C1.2, C2.2, C3.2, C4.2, C5.2, C6.2, C7.2, C8.2, C9.2, C10.2, C11.2, C12.2, C13.1, C15.2, C17.2, C18.2, C19.2, C20.2, C21.2, C22.2, C23.2, C24.2, C25.2, C26.2, C27.1, C28.2, C29.2, C32.2, C33.2, C34.2, C36.2, C38.2, C39.1, C40.2, C41.2, C42.2, D1.2 (A2), J1.A1 (GND), J1.A12 (GND), J1.B1 (GND), J1.B12 (GND), J1.S1 (SHIELD), J2.2, J2.MP (MountPin), R3.2, R7.2, R13.2, R14.2, R15.2, R21.2, R25.2, R29.2, R30.1, R36.2, TP5.1 (1_1), TP9.1 (1_1), TP16.1 (1_1), TP23.1 (1_1), TP24.1 (1_1), U1.12 (VSSA), U1.18 (VSS), U1.63 (VSS), U2.2 (RESV_2), U2.3 (RESV_3), U2.6 (GND), U2.7 (RESV_7), U2.9 (INT2/FSYNC/CLKIN), U2.10 (RESV_10), U2.11 (RESV_11), U3.4 (DGND), U3.20 (AGND), U3.23 (PGND), U3.29 (EP), U4.4 (GND), U5.4 (GND), U5.9 (GND), U7.4 (GND), U8.1 (GND), U8.7 (GND), U9.1 (GND), U9.7 (GND), Y1.2 (GND), Y1.4 (GND), Y2.2 (GND), Y2.4 (GND)
MOTOR1: J2.5, U1.37 (PC6)
MOTOR2: J2.6, U1.38 (PC7)
MOTOR3: J2.7, U1.39 (PC8)
MOTOR4: J2.8, U1.40 (PC9)
unnamed: C14.1, R5.2
unnamed: C30.1, R18.2
unnamed: D4.1 (K), R15.1
unnamed: D5.1 (K), R14.1
unnamed: D6.1 (K), R29.1
unnamed: D7.1 (K), R31.1
unnamed: D8.1 (K), R32.1
unnamed: J1.A5 (CC1), R3.1
unnamed: J1.B5 (CC2), R36.1
unnamed: J1.A6 (D+), J1.B6 (D+), R2.1
unnamed: J1.A7 (D-), J1.B7 (D-), R1.1
unnamed: R6.2, R7.1, R8.1
unnamed: R20.2, R21.1, R22.1
unnamed: C40.1, R35.2, U1.7 (NRST)
unnamed: C39.2, R28.2, R30.2, U1.10 (PC2)
unnamed: C11.1, U1.5 (PH0), Y1.1
unnamed: C10.1, U1.6 (PH1), Y1.3
unnamed: C2.1, U1.31 (VCAP_1)
unnamed: C1.1, U1.47 (VCAP_2)
unnamed: U3.5 (CLKIN), Y2.1
unnamed: U3.7 (CLKOUT), Y2.3
unnamed: R4.1, U4.1 (PG)
unnamed: C14.2, L3.1, U4.3 (SW)
unnamed: C13.2, U4.7 (VCC)
unnamed: R19.1, U7.1 (PG)
unnamed: C30.2, L4.1, U7.3 (SW)
unnamed: C27.2, U7.7 (VCC)
PA4: R33.2, U1.20 (PA4), U2.12 (AP_CS)
PA5: U1.21 (PA5), U2.13 (AP_SCL/AP_SCLK)
PA6: U1.22 (PA6), U2.1 (AP_SDO/AP_AD0)
PA7: U1.23 (PA7), U2.14 (AP_SDA/AP_SDIO/AP_SDI)
PB2: U1.28 (PB2), U2.4 (INT1/INT)
PB8: A1.8 (SCLK), R27.2, U1.61 (PB8)
PB9: A1.7 (SDI/SDA), R26.2, U1.62 (PB9)
SA: TP18.1 (1_1), U1.29 (PB10)
TELEM: J2.4, U1.54 (PD2)
UART1 RX: TP10.1 (1_1), U1.59 (PB7)
UART1 TX: TP13.1 (1_1), U1.58 (PB6)
UART2 RX: TP7.1 (1_1), U1.17 (PA3)
UART2 TX: TP8.1 (1_1), U1.16 (PA2)
UART4 RX: TP11.1 (1_1), U1.15 (PA1)
UART4 TX: TP12.1 (1_1), U1.14 (PA0)
USB VBUS: D2.2 (A), J1.A4 (VBUS), J1.A9 (VBUS), J1.B4 (VBUS), J1.B9 (VBUS)
VIN: C12.1, C17.1, C28.1, C29.1, C41.1, C42.1, D1.1 (A1), J2.1, R4.2, R10.1, R19.2, R28.1, U4.2 (IN), U7.2 (IN)
VOUT: C35.1, U3.26 (VOUT)

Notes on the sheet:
GYRO PWR
CAM
OSD OSC
GYRO
LDO/BUCK STATUS LED
OSD PWR
COMM
BOOT
PADS
BARO I2C
MCU DECOUPLING
FC VIN
SPI OSD
OSD
9V BUCK
BF STATUS
SPI FLASH
VTX
SPI GYRO
OSD I/O
LDO
GYRO INT
BARO
5v Buck
UART1 AND 3 NO 4V5
DECOUPLING CAPS
USB

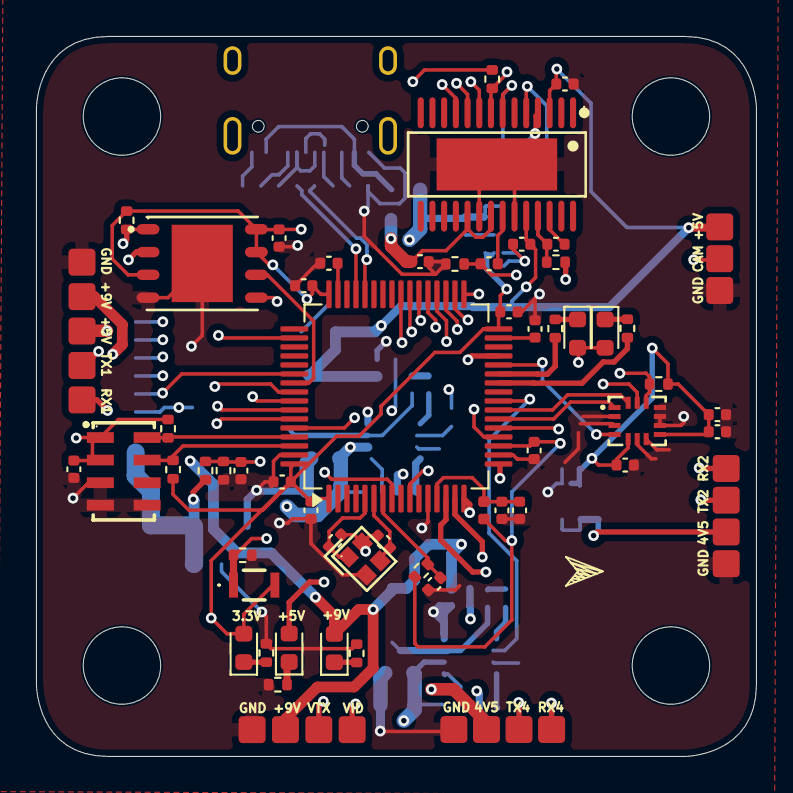
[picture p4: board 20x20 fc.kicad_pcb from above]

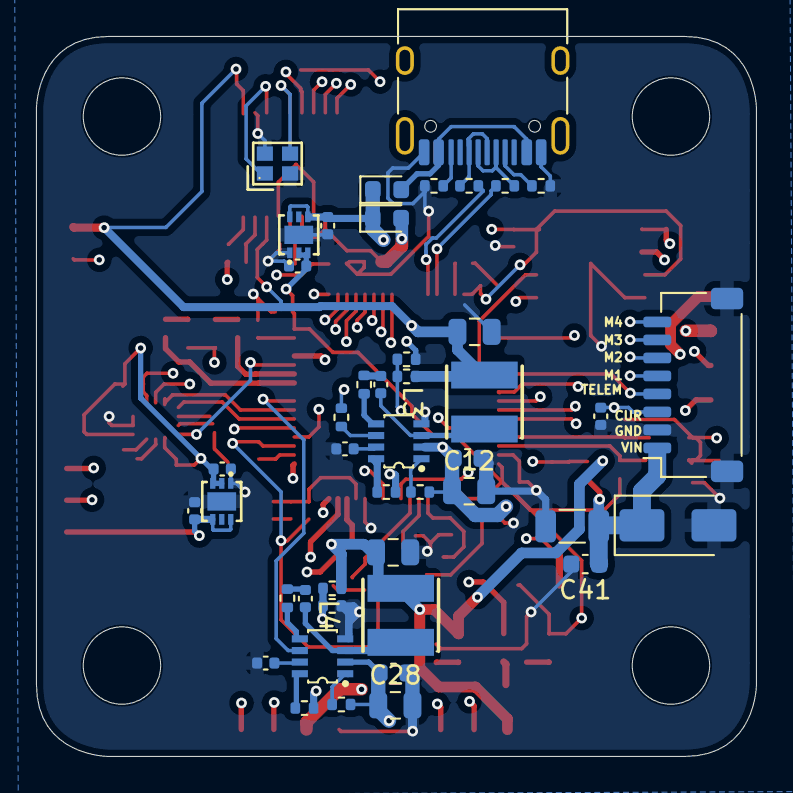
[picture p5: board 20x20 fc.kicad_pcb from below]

Board: 6 copper layers, 40.0 x 40.0 mm, 120 parts (44 on the bottom side), 80 nets.

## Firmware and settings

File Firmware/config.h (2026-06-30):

/*
 * This file is part of Betaflight.
 *
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
 * See the GNU General Public License for more details.
 *
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
 * If not, see <http://www.gnu.org/licenses/>.
 */

#pragma once

#define FC_TARGET_MCU     STM32F405
#define BOARD_NAME        yecnodF405
#define MANUFACTURER_ID   CUST

#define USE_GYRO
#define USE_GYRO_SPI_ICM42688P

#define USE_ACC
#define USE_ACC_SPI_ICM42688P

#define USE_BARO
#define USE_BARO_MS5611

#define USE_FLASH
#define USE_FLASH_W25Q128FV
#define USE_MAX7456

#define MOTOR1_PIN           PC6
#define MOTOR2_PIN           PC7
#define MOTOR3_PIN           PC8
#define MOTOR4_PIN           PC9

#define UART1_TX_PIN         PB6
#define UART1_RX_PIN         PB7
#define UART2_TX_PIN         PA2
#define UART2_RX_PIN         PA3
#define UART3_TX_PIN         PB10
#define UART4_TX_PIN         PA0
#define UART4_RX_PIN         PA1
#define UART5_RX_PIN         PD2

#define I2C1_SCL_PIN         PB8
#define I2C1_SDA_PIN         PB9



#define SPI1_SCK_PIN         PA5
#define SPI1_SDO_PIN         PA7
#define SPI1_SDI_PIN         PA6
#define GYRO_1_CS_PIN        PA4
#define GYRO_1_EXTI_PIN      PB2	
#define GYRO_1_SPI_INSTANCE	 SPI1


#define SPI2_SCK_PIN         PB13
#define SPI2_SDI_PIN         PB15
#define SPI2_SDO_PIN         PB14
#define MAX7456_SPI_CS_PIN   PB12
#define MAX7456_SPI_INSTANCE SPI2

#define SPI3_SCK_PIN         PB3
#define SPI3_SDI_PIN         PB4
#define SPI3_SDO_PIN         PB5
#define FLASH_CS_PIN         PA15
#define FLASH_SPI_INSTANCE   SPI3


#define ADC_VBAT_PIN         PC2
#define ADC_CURR_PIN         PC0

#define LED0_PIN             PB1
#define LED1_PIN             PB0


#define TIMER_PIN_MAPPING \
    TIMER_PIN_MAP(0, MOTOR1_PIN, 2, 0) \
    TIMER_PIN_MAP(1, MOTOR2_PIN, 2, 1) \
    TIMER_PIN_MAP(2, MOTOR3_PIN, 2, 1) \
    TIMER_PIN_MAP(3, MOTOR4_PIN, 2, 0) \

#define ADC3_DMA_OPT 1
#define ADC_INSTANCE ADC3

#define BARO_I2C_INSTANCE I2CDEV_1

#define DEFAULT_BLACKBOX_DEVICE BLACKBOX_DEVICE_FLASH
#define DEFAULT_DSHOT_BITBANG           DSHOT_BITBANG_OFF

#define DEFAULT_CURRENT_METER_SOURCE CURRENT_METER_ADC
#define DEFAULT_VOLTAGE_METER_SOURCE VOLTAGE_METER_ADC
#define DEFAULT_VOLTAGE_METER_SCALE 110
#define SYSTEM_HSE_MHZ 16

#define ESC_SENSOR_UART      SERIAL_PORT_UART5

#define PINIO1_PIN PC4
#define PINIO1_BOX     40
#define PINIO1_CONFIG  129
#define BOX_USER1_NAME "10V BEC"

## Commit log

2026-05-17 Add project notes and BOM information to README
    Added notes about the project experience and BOM status.
2026-05-17 Add project notes and update image section
    Added notes about project experience and BOM completeness.
2026-05-17 Fix links and formatting in BOM section
    Updated links for solder paste, squeegee, and flux paste entries.
2026-06-30 Add schematic PDF link and update cost section
    Updated README to include schematic PDF link and revised content.
2026-06-30 Clean up BOM section and project notes in README
    Removed detailed BOM entries and notes from the README.

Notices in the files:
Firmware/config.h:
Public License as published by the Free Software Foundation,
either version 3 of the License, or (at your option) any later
